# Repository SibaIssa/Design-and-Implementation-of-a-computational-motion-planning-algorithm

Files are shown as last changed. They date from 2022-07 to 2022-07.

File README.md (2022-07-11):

# Design-and-Implementation-of-a-computational-motion-planning-algorithm-based-on-navier-stokes-equations
This repositoery is based on the graduation project for Bachelor Degree in Mechatronics Engineering at Tishreen University, Syria - Summer 2021

## Abstract
Formation of non-holonomic swarm robots has received a lot of considerations in both academia and
industry over last two decades. Many path planning methods produce collision-free paths for a group of
multiple robots, but many of them are computationally expensive and complex to implement and develop.
In addition, these methods do not find a solution in all environments, or they find a solution that is not
optimal. In this project, we present a computational motion planning algorithm based on fluid dynamics
PDE for Robotic Swarms. This proposed method features a computationally cheap algorithm, and it is
easy to develop using updated tools and hardware. But, most importantly, it always ensures finding a
path, because partial differential equations of fluid dynamics always finds a solution that describes the
movement of the fluid’s particles towards a goal. The aforementioned feature gives this algorithm a clear
advantage because it is reliable, and it produces a smooth path. The validity of this algorithm will be
tested on a robotic swarm platform that we designed and implemented to ensure high quality and ease of
use. The control of the swarm is preformed centrally, and a visual feedback is provided continually to the
central computer from a camera that is fixed above the robots.

## Environment Setup
In the end we will have a square platform (**4.2×4.2 [m²]**) with high walls and different types of obstacles. Above the platform there is a fixed **stereo camera**, and inside the platform there will be a **15 mobile robots**. We will design everything from scratch then we will test our proposed path planning algorithm on our designed platform. And this is a 3D design for the platform:

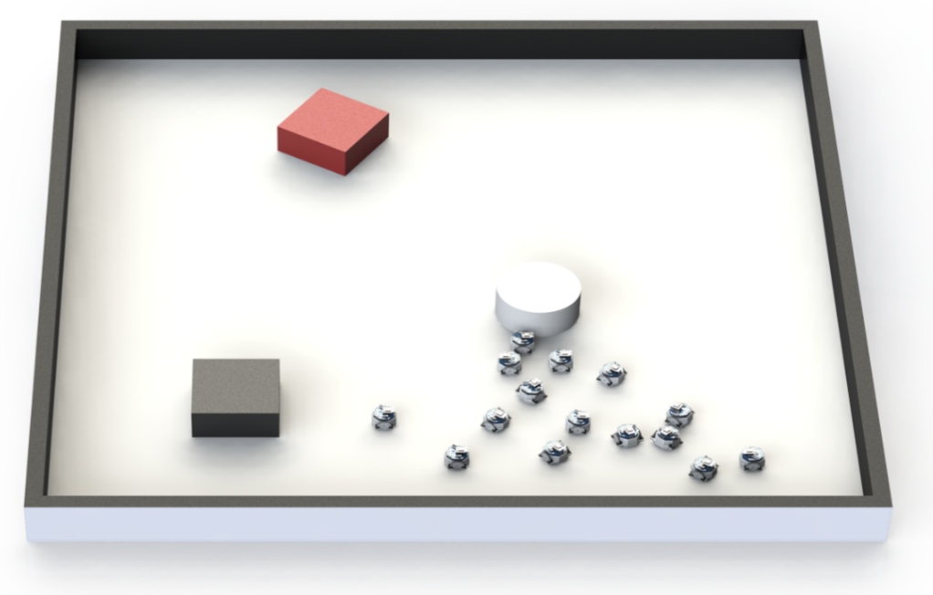
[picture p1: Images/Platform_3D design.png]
platform


## Project overview

### Designing Stage:

After many designs, we ended up with the octagon-shaped robot with two circuits (each one of them has two layers). We chose this design; because it was the most compact one. We used **SolidWorks** for designing the body while we used **Altium** for the circuits. 

- circuits PCB design (the left circuit is the top one while the right circuit is the bottom one):

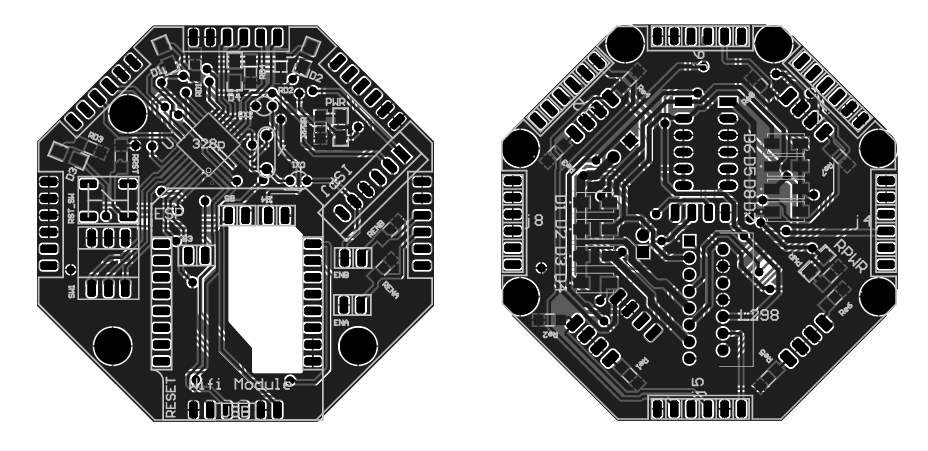
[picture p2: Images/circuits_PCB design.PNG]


- We can see below the body CAD design with the wheels in which we chose them like this to make our own encoder and it is important to mention that we chose the optimum number of the holes (33 holes):

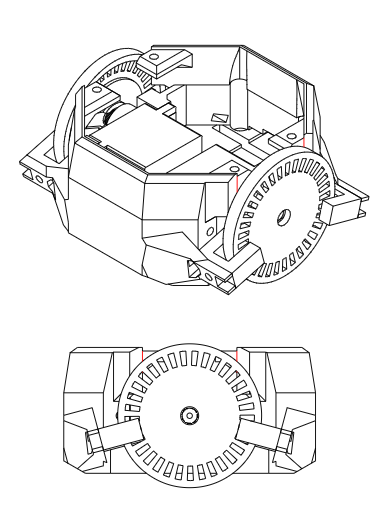
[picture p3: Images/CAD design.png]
CAD


- robot top-view:

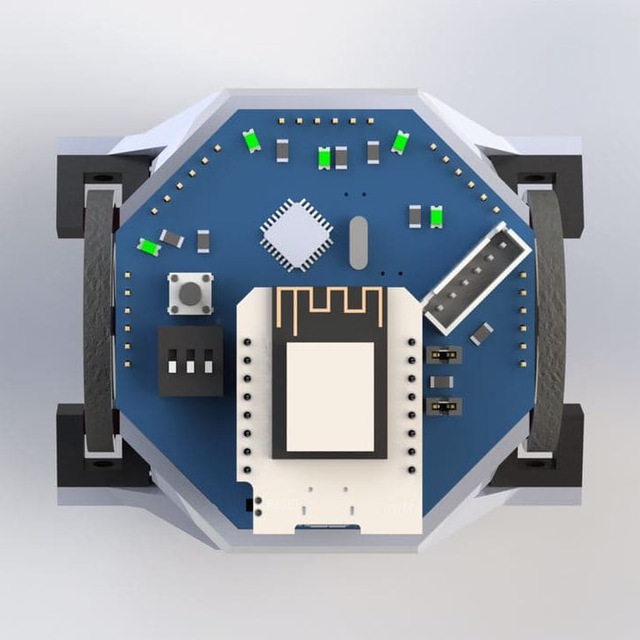
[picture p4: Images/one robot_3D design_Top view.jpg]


### Manufacturing stage:
After the designing stage, we started printing the bodies and the wheels by using a 3D printer (we used Acid Polylactic with PLA as a material). And we were printing the circuits in parallel.

- circuits after manufacturing:

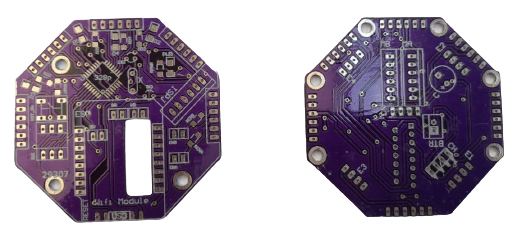
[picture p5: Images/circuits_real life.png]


- we can see below one robot after manufacturing and assembling, and for more images about manufacturing stage you can check the [Images Folder](https://github.com/SibaIssa/Design-and-Implementation-of-a-computational-motion-planning-algorithm/tree/main/Images).

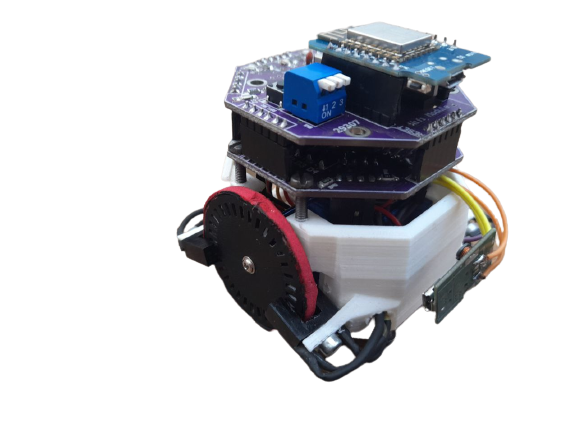
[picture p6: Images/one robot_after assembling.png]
robot


### Algorithm Implementation
- We started in simulation; we implemented the PDE algorithm for one robot and tested it on different maps by using **MATLAB**. And as we can see below the PDE algorithm managed to find a path from the start point to the goal in each map:

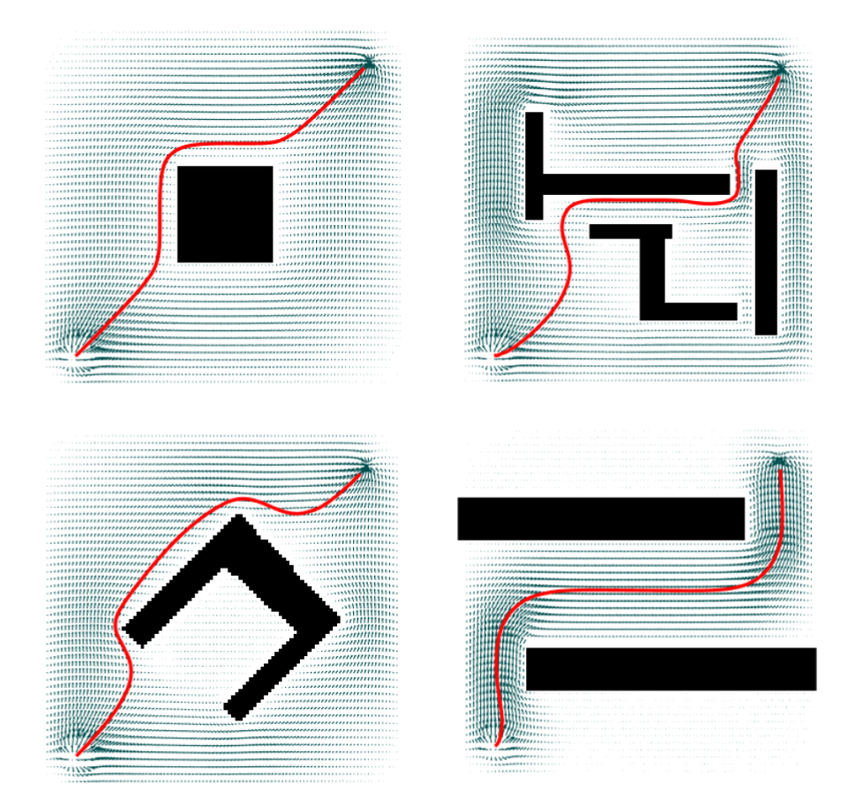
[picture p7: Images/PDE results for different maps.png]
different_maps


As it is clear from the previous image; the PDE managed to find the path for any given map which gives it advantages over the most popular path planning algorithms (A*, Dijkestra and potential field) in terms of finding the path and time consumption.

- Then we started the impelmentaion in real life:
1. We calibrated the camera depeding on the pinhole camera model and we found the Intrinsic and Extrinsic parameters.
2. We used Aruco markers in order to identify each robot, and each robot has its own ID through the whole project; in which it will help us later in sending a specific message for each robot.
3. After working onthe feedback system, we started working on ROS on the central computer. We created three nodes each one has it is clear task -as it is clear below- then we connected the central computer with each robot wirelessly by using esp8266 chip.

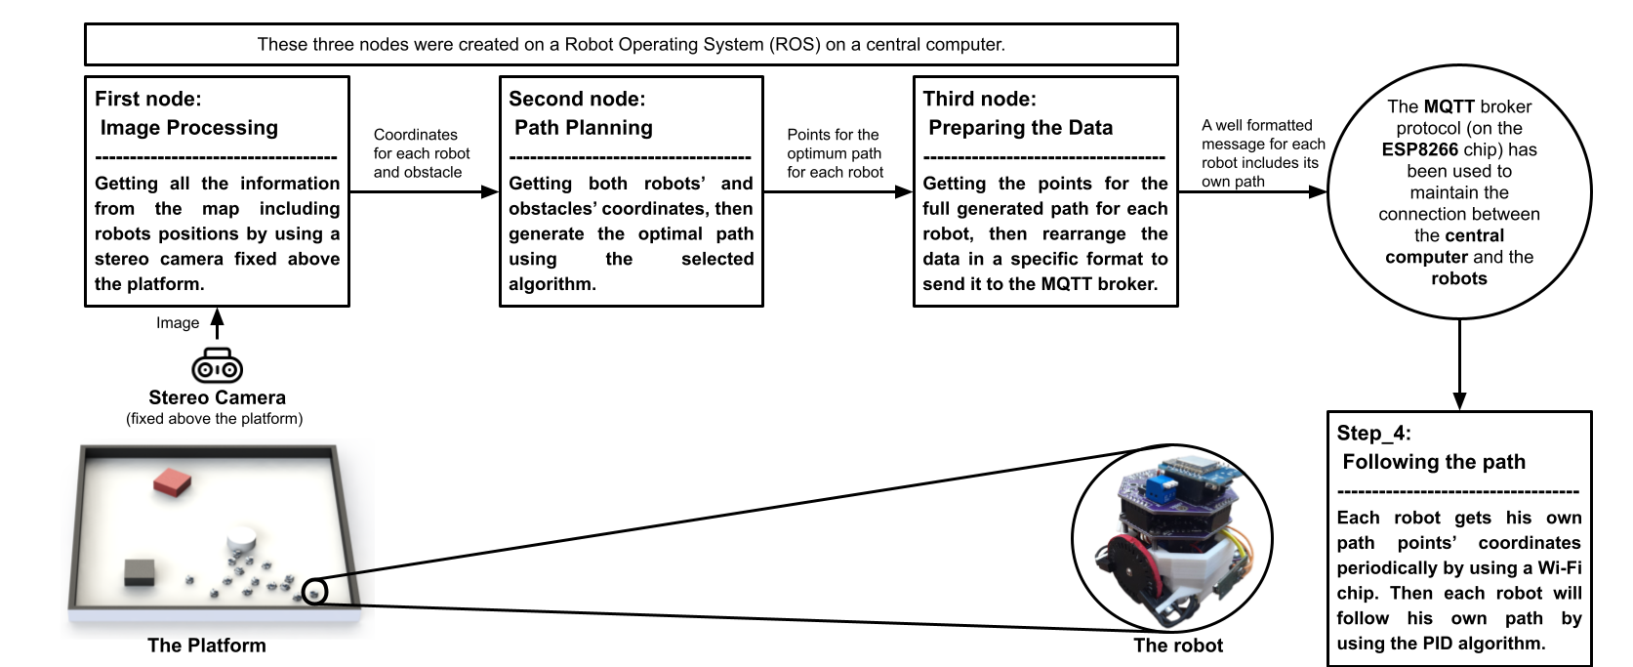
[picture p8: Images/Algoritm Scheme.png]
here the project scheme:
 
## Project output
1. Platform (**4.2×4.2 [m²]**) with high walls and different types of obstacles.
2. **15 octagon-shaped mobile robots**  designed from scratch with dimensions (**6×7×6 [m³]**).
3. Implementing a computational motion planning algorithm on a single robot, then developing it and expanding it for the swarm of robots.
4. Comparing between our suggested algorithm and the famous algorithms in the literature (A*, Dijkstra, Potential Field) 
5. Extracting results that confirm the validity of the proposed algorithm and its superiority over conventional and non-traditional algorithms in terms of path-finding inevitability and other factors. You can check the following video:

https://user-images.githubusercontent.com/51207510/178347807-7e33a0b5-0230-4640-b8dc-26850cdf5a6b.mp4

## Files
- [Body Design Folder:](https://github.com/SibaIssa/Design-and-Implementation-of-a-computational-motion-planning-algorithm/tree/main/Body%20Design)
includes **SolidWorks** files.
- [Circuits PCB Design Folder:](https://github.com/SibaIssa/Design-and-Implementation-of-a-computational-motion-planning-algorithm/tree/main/Circuits%20PCB%20Design)
includes the **PCB** files for both top and bottom circuits, and it is important to metion that we used **Altium** software for designing the circuits.
- [Swarm Robot Firmware Folder:](https://github.com/SibaIssa/swarm-robot-firmware) includes **.cpp** files in which contain the code that we put it on the microcontroller on each robot, and we used **AVR** software for programming.

## Credits
I worked on this project with two of my colleagues:
- [Adnan Saood](https://github.com/adnan-saood)
- [Nada Salman](https://www.linkedin.com/in/nada-s-salman/)

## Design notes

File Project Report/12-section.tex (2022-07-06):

لإيجاد مواقع الروبوتات سوف يتم استخدام نظام التعريف ArUco، حيث تتم طباعة عدة QR codes ولصقها على سطح كل روبوت. بعد القيام بعملية معايرة لبارامترات الكاميرا الـIntrinsic والـExtrinsic يمكن أيجاد المصفوفة $ \mathbb{C} $ المستخدمة في \ref{eq:cameramatrix}.

\begin{equation}\label{eq:cameramatrix}
\mathbb{P}=\left(\begin{matrix}p_x\\p_y\\1\\\end{matrix}\right)=\mathbb{C}\times\left(\begin{matrix}r_x\\r_y\\r_z\\1\\\end{matrix}\right)=\mathbb{C}\times\mathbb{R}
\end{equation}
حيث يمثل $ \mathbb{P} $ موضع الروبوت في إحداثيات حساس الكاميرا، و$ \mathbb{R}  $إحداثيات الروبوت في الاحداثيات الأرضية، و$  \mathbb{C}  $ مصفوفة الكاميرا (Camera Matrix).

منها يمكن نقل كل بكسل من بكسلات الكاميرا الى الاحداثيات الأرضية باستخدام الـpseudo-inverse للمصفوفة $\mathbb{C}$. نذكر هنا أن المصفوفة $ \mathbb{C} $ :

\begin{equation}
\mathbb{C}=\mathbb{K}\times\left(\mathbb{R}\ |\ {T}\right)
\end{equation}

حيث تمثل المصفوفة $ \left(\mathbb{R}\ |\ {T}\right)  $ التحويل المتجانس الذي ينقل $ \mathbb{R}  $ الى احداثيات الكاميرا، والمصفوفة $ \mathbb{K}  $ تقاس من بارامترات العدسة والحساس وتشكّل كالتالي:
\begin{equation}
\mathbb{K}=\left(\begin{matrix}f_x&0&0\\s&f_y&0\\c_x&c_y&1\\\end{matrix}\right)
\end{equation}

يمثل كل من $ f_x, f_y $ البعد البؤري للعدسة، وs معامل انحراف الحساس، و $c_x, c_y$ يمثلان مركز الحساس بوحدات البكسل.
نذكر هنا أنه من الواجب القيام بعملية معايرة تسبق مرحلة نقل كل نقطة من نقاط الكاميرا الى الاحداثيات الواقعية وذلك لتقريب الكاميرا الموجودة أقرب ما يمكن الى نموذج الـ pinhole\ camera الموجود في المعادلات السابقة.

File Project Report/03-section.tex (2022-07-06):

تعد مضمنات هذا البحث أحد القضايا التي تطرق لها الباحثون بكثرة واهتمام في الفترة الأخيرة: التشكيل السرابي للروبوتات غير الهولنومية.  هناك العديد من الطرق التي قد توصل مجموعة من الروبوتات من منطقة الى أخرى في فضاء العمل بسلام (أحياناً)، لكن عديدها إما تحوي تعقيدات برمجية وبنية خوارزمية ومخطط حالة غاية في التعقيد، أو أنها لا توفر حل في أغلب الأحوال. نحاول في هذا البحث تقديم خوارزمية تخطيط مسار لسرب من الروبوتات الغير هولنومية في بيئة مكتظة باعتبارها تابعة بالحالة للحل الرقمي لمعادلة جريان المائع من منطقة إلى الأخرى بشكله المستقر.
من مزايا الحل المقدم أنه رخيص حسابياً ويمتلك العديد من العناصر القابلة للتسريع باستخدام أدوات حسابية وعتاد حاسوبي جديد، لكن محور البحث يكمن في مكان آخر. نحاول في هذا البحث تقديم طريقة حتمية لإيجاد مسارات حركة هذه الآليات من منطقة لأخرى في فضاء العمل، فالمعادلات الرياضية لجريان السوائل حتماً ستجد حلاً يقوم بإيصال جزيئات المائع من المنطلق للهدف. هذه الحتمية ستعطي أفضلية واضحة للطريقة المقترحة لسببين: موثوقية الطريقة (إذا كان الوصول ممكن فهو حتماً ضمن مجموعة الحل)، ونعومة المسارات المنتجة (مما سيمكن الآليات الغير هولنومية من تقليص الفارق العتادي مع الهولنومية).
سيتم اختبار طريقة الحل المقترحة على منصة روبوتات قمنا بتصميمها وتنفيذها بشكل كامل، مع مراعاة عوامل مثل جودة التصنيع والمرونة والسهولة في الاستخدام والتعديل والتكلفة المناسبة. تم تصميم المنصة بحيث أن يتم التحكم والتواصل مع الروبوتات بواسطة حاسوب مركزي ويتم مراقبتها بواسطة كاميرا مُثبتة أعلى المنصة.

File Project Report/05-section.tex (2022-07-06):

إنّ مفهوم الأسراب مأخوذ من الطّبيعة، حيث تمّت محاكاة أسلوب التّعاون بين الأسراب البيولوجيّة (النّمل، النّحل، الأسماك..) ونُقل هذا المفهوم إلى الرّوبوتات. يمكننا تصنيف الأسراب البيولوجيّة إلى أسراب أرضيّة وأخرى جويّة، وكذلك الأمر بالنّسبة للرّوبوتات. يختلف هذان النّوعان فيما بينهما من ناحية التّطبيق بشكل أساسي وقد اعتمد البحث \cite{b1} على تصنيف التطبيقات حسب نوع المهمّة الّتي تتولّاها الرّوبوتات (تغطية منطقة ما، مهمّات خطيرة، مهمّات يلعب الوقت فيها دور أساسي...).
يعدّ تخطيط المسار الحسابي للروبوتات الأرضيّة مشكلة مطروقة جداً في الوقت الحالي لما لها من أهمية في توفير الوقت، الطاقة، والعتاد الحسابي. حسابياً، إنّ مشكلة تخطيط المسار الأمثل لأي آلية هي مسألة \textenglish{NP-Hard} \cite{b2,b3}. تتعقد أليات الحساب وتبعاته عند التعامل مع بيئة ديناميكية، أو عند القيام بتخطيط مسار أكثر من كائن في ذات الوقت.
يهدف المشروع الى البحث في إمكانية تطوير آليات لتخطيط المسار الحسابي لمجموعة كائنات اعتماداً على معادلات الجريان النّاتجة عن حل المعادلات التّفاضلية الجزئيّة لحركة الموائع. لقد قدّم كلّ من نافيير وستوكس معادلات كافية لنمذجة حركة السائل في الظروف المُختلفة، وسيتمّ الاعتماد عليها في إنشاء المسارات.

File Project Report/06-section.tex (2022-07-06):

يقدم هذا القسم مجمل ما تم مراجعته بهدف تصميم وتنفيذ خوارزمية البحث والمنصّة الفعالة.

\subsection{التصنيف والتصميم}

إنّ الأنظمة متعدّدة الروبوتات تلاقي اهتماماً كبيراً في المراجع ولاسيّما في الآونة الأخيرة؛ نظراً إلى أنّ مجالات التّطبيق والمهام الّتي تواجهها تزداد تعقيداً. لقد تمّ اقتراح تصنيف جديد في عام 2004 اعتماداً على ثلاث نقاط أساسيّة: (1) عقلانيّة التّصميم، (2) الوظائف التّقنيّة الاساسيّة (لكّل من العتاد الصّلب والبرمجيّات)، (3) المهمّات الّتي يجب أن تقوم الرّوبوتات بتنفيذها. حيث تمّ التّصنيف على عدّة مستويات ضمن فئتين أساسيّين: الأبعاد التنسيقيّة، وأبعاد النّظام كما هو موضّح في الجدول \ref{06:table:1} \cite{b4}. 

\begin{table}[]
	\begin{tabular}{|l|l|}
		\hline
		الأبعاد التّنسيقيّة Coordination Dimensions & أبعاد النّظام System Dimensions       \\ \hline
		التّعاون   Cooperative                      & الاتّصال   Communication              \\ \hline
		المعرفة Knowledge                           & تكوين   الفريق team Composition       \\ \hline
		التّنسيق   Coordination                     & هيكليّة   النّظام System Architecture \\ \hline
		التّنظيم Organization                       & حجم الفريق Team Size                  \\ \hline
	\end{tabular}
\caption{الأبعاد التنسيقية وأبعاد النظام}
\label{06:table:1}
\end{table}

وفي العام التّالي طرحت الورقة البحثيّة \cite{b5} تبين أنّ أي فعل يقوم به أي روبوت يَأخذ بالحسبان الأفعال الّتي تقوم بها بقيّة الرّوبوتات، وهكذا ينتج مجموعة من الرّوبوتات الّتي تعمل باتّساق لتحقيق أفضل أداء ممكن. وقد أظهرت هذه الآليّة من التّنسيق أداء عالٍ؛ حيث تمكّنت الروبوتات من اكتشاف بيئتها في وقت أقل مقارنةً مع المنهجيّات الأخرى الّتي لا تعتمد على التنسيق بين الرّوبوتات بشكل صريح. وبالرّغم من النّتائج الجيّدة الّذي حقّقها النّهج المتّبع في البحث \cite{b5}، إلّا أنّ هناك بعض النقاط الّتي تحتاج إلى تطوير، حيث يجب مناقشة الحالات الّتي يتمّ فيها تعطّل أحد الرّوبوتات أو حدوث تغيّر ما في البيئة المحيطة بها.

ومن ناحية أخرى، نالت أعداد الرّوبوتات الّتي تشكّل السّرب اهتماماً كبيراً في مجال البحث العلميّ. على الرّغم من أنّ سلوك كلّ روبوت على حدا يُعدّ سلوكاً بسيطاً، إلاّ أنّه عندما تعمل هذه الرّوبوتات معاً يصبح سلوكها أكثر تعقيداً. أشار \cite{b6} إلى أنّ فهم الرّوبوتات بشكل فرديّ هو أمرٌ سهل، أمّا بالنّسبة لتوقّع سلوكها معاً فهو أمرٌ صعب المنال. لقد تمّ عرض النّهج المعتمد من قبل \cite{b6} من خلال التّحليل العميق لخوارزميّة السّرب المُتّبعة والنّموذج الاحتمالي المُرتبط بها؛ حيث تمّ فحص خوارزميّة التّحكم باستخدام فضاء الحالة المُطوّرة من قبل \cite{b7} على مجموعة من الرّوبوتات الباحثة عن طعام.

 لقد قام \cite{b6} باستخدام خوارزميّة ألفا في شبكة الاتّصال اعتماداً على المنطق الزّمني $ (Temporal logic) $، حيث تمّ التّركيز على حالة الرّوبوتات بدلاً من الموقع وتفاصيل حركة كلّ روبوت. ولكنّ وبالرّغم من النّتائج المُرضية وصل اليها البحث، إلا أنه لم يتمكّن من إجراء عملية التّحليل سوى على عدد قليل من الرّوبوتات بسبب مشكلة انفجار الحالة $ (state explosion) $ التي ظهرت أثناء عمليّة فحص النّموذج الرّياضي. 
 
 \subsection{تخطيط المسار}
 
 تُعدّ مشكلة تخطيط المسار متعدد الروبوتات مشكلة معقدة حسابياّ لأنّ صعوبة الحساب تنمو مع عدد الروبوتات. إنّ وجود قيود وعوائق في المسار يولّد مشكلة كبيرة، ومن هنا بدأت عمليّة البحث عن خوارزميّات لحلّ هذه المشكلة. أحد الخوارزميّات المُتّبعة لحلّ مشكلة المسار المقيّد هي الـ \textenglish{Visibility Graph (VG)}. تبدأ هذه الطريقة بتشكيل الرّسم البياني عن طريق رسم العقد (Nodes) والحواف (Edges) باستخدام تقنيّة التّصوير بالأشعّة، ومن ثمّ تحديد البيان الموجّه. يتمّ بعد ذلك إيجاد المسار الأقصر باستخدام خوارزميّات إيجاد الطريق الأقصر في البيان. نذكر هنا أن المسار النّاتج عادةً قريب جدّاً من العوائق.
 
 وكان البحث \cite{b8} قد قدّم عام 1985 طريقة فريدة لتفادي العوائق اعتماداً على تقنيّة الـ $ (Potential Field) $، حيثُ تمّ التّحكم بالروبوتات على عدّة مستويات وبالزّمن الحقيقي. وتتميّز هذه الطريقة بإمكانيّة توسيع الحلّ ليشمل البيئات ذات العوائق المُتحرّكة باستخدام حقل كموني متغيّر مع الزّمن.  وفي عام 2006 قدّم العمل \cite{b9} طريقة حقل كموني لتخطيط مسار الروبوت بالاعتماد على ناتج جمع تابعين هما: تابع $ (repulsive) $ الذي يتجنب المسارات القريبة من العوائق، وتابع $  (Attractive) $ قيمته تتعلق بالمسافة عن الهدف.
 
 إنّ طريقة الـ $ potential field $ هي طريقة مباشرة لحساب الحقل المتجهات $ (vector field) $ اعتماداً على موقع الهدف والعوائق، ولكنها تتطلّب روبوتات مُتحكّم بها بشكل كامل (قادرة على التّحرك بأي اتّجاه بشكل آني). على خلاف الحقل الكموني، طرق تخطيط المسار المعتمدة على الدّوال التّدفقيّة $ Stream function $ لا تتطلب التّحكم ذلك، كما أنّها تضمن تحوّل جميع نقاط التّوازن إلى نقاط سرجيّة، مما يعني ضمان وصول الروبوت إلى هدفه. لقد أظهرت عمليّة تخطيط المسار المُعتمدة على الدّوال التّدفقيّة المطروحة في \cite{b10} فعاليّة وسرعة عاليّة في التّكيف مع التّغيرات في الشّروط. على عكس طرق تخطيط المسار الأخرى، الطّرق الّتي تعتمد على الدّوال تتميز بمظهرها الحدسيّ بالنّسبة لمراقب الخارجي. إنّ وجود أكثر من حاجز لا يضمن دائماً الحصول على نتائج صحيحة، لكن هذا المثال يوضّح أن السلوك لا يزال مقبولاً كما هو موضح في الشكل \ref{06:fig:1}.
 \begin{figure}[h]
 	\centering
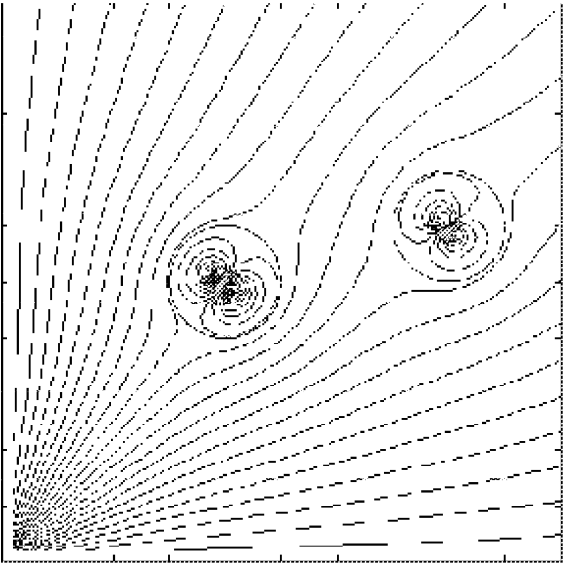
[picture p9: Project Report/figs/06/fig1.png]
 	
 	\caption{مثال على الدوال التدفقية}
 	\label{06:fig:1}
 \end{figure}

في عام 2015 تمّ طرح سلالات فورونوي \textenglish{VORONOI STRAINS} كخوارزميّة جديدة لتخطيط المسار والّتي حقّقت فائدة مهمّة على صعيد البيئات المعقّدة \cite{b9}. لقد حقّقت هذه الخوارزميّة نتائج مثيرة للاهتمام في مساحات عمل فيها عدد كبير من العوائق، فقد أظهرت حلولاً أفضل بكثير من خوارزميّة PSO البسيطة والمُطوّرة من أجل نفس عدد التّكرارات. إضافة إلى ذلك، أثبتت أنّها أكثر صلادة وأقل اعتماديّة على الحالة الابتدائيّة (العشوائية). كما تتميّز هذه الخوارزميّة باحتماليّة أكبر لتجنّب النّقاط الصّغرى المحليّة، ولكن قد أثبتت التّجارب أن عمليّة االأمثلة هذه غير مُجدية مالم تكن البيئة معقّدة بشكل كافِ.

أثناء تخطيط الحركة يمكننا تصنيف العمل إلى صنفين أساسيّن؛ فإمّا أن يتمّ تخطيط المسار بشكل كامل قبل البدء بالحركة (offline)، أو أن تتمّ عمليّة التّخطيط بشكل تدريجي أثناء الحركة (online).

  في \cite{b11} ، تم التّركيز على تخطيط المسار بشكل كامل قبل بدء الحركة، بالإضافة إلى وجود حواجز ثابتة، وهي إحدى الأمور الّتي أعطت هذا البحث محدوديّته. تتميّز طريقة تخطيط المسار المُقترحة في \cite{b11} بأنّها تمكّننا من الحصول على مسار ثلاثي الأبعاد مثالي يمكن الروبوتات من التحليق على ارتفاعات منخفضة في بيئة ذات تضاريس مُعقّدة.
  
  وفي عام 2020 طُرحت الورقة البحثيّة \cite{b12} بهدف توجيه روبوتات طائرة في مجال جوّي مفتوح وتضاريس غير معلومة لتتفوق بذلك على البحث \cite{b11} وذلك عبر حلّ معادلة الاستمراريّة للموائع. لقد حقّقت هذه الدّراسة وقتاً أقلّ من أربع طُرق أخرى $( A*, Dijkstra, DP, PE) $.
  
  إضافة إلى الخوارزميات التقليدية، العديد من الدراسات أظهرت نتائج خوارزميات التعلم الآلي لحل هذه النوع من المشكلات. في \cite{c1} تم استخدام الشبكات العصبونية الالتفافية لتحسين حلول الخوارزميات التقليدية كما نجد في \cite{c2} أنه تم استخدام خوازرمية تعلم Q-learning معتمدة على الخوارزمية المحسنة \textenglish{improved particle swarm optimization}. تهدف الخوارزميات المستخدمة الى تقليل طول المسار وزمن الوصول وزوايا دوران الروبوتات لتقليل استهلاك الطاقة. تمت المقارنة بين اربع خوارزميات وايجاد النتائج باختلاف عدد الروبوتات في السرب هي CQL و PSO وIPSO-DV  و QIPSO-DV وأظهرت النتائج تفوق QIPSO-DV على باقي الخوارزميات كما يمكن ملاحظة تراجع أداء هذه الخوارزمية مع زيادة عدد الروبوتات ولاسيما من حيث زمن التنفيذ وعدد التكرارات اللازمة للوصول الى الحل الأمثل (إن وجد) .
  في \cite{c3} تم اقتراح تقسيم الخريطة الكلية الى خرائط بيان جزئية sub-graphs مع قيود على الدخول والخروج من كل خريطة وذلك لضمان إيجاد المسار. بعد التجريب، تم التوصل الى حل فعال وسريع نسبيا لكنه لا يضمن ايجاد مسار أمثل وبحاجة إلى عمليات معالجة لاحقة لتقليل المسافات الضائعة.  
  
   يعد موضوع انشاء طريق باستخدام الحل الرقمي للمعادلات التفاضلية الجزئية موضوع حديث عالمياً ويحتاج الكثير من العمل، قدمت واحدة من الأبحاث القائمة على موضوع استغلال جريان السوائل في توليد المسار عام 2017، حيث تهدف \cite{b13} الى انشاء المسار الأفضل لحركة سفينة باستخدام طريقة $ lattice Boltzmann $ الرقمية. البحث لم يناقش آلية انشاء طريق من نقطة إلى اخرى في فضاء العمل، بل ناقش عبور منطقة تحتوي عوائق بشكل عام. إضافة لذلك، فإن الحل الرقمي باستخدام $ lattice Boltzmann $ لم ينتج حقول متجهات سرعة تحمل نفس السلوك الفيزيائي للسوائل، يمكن التحقق من ذلك بالنظر في سلوك الحقل عند الحواجز في الشكل \ref{06:fig:2}.

   \begin{figure}[htbp]
   	\centering
   	\includesvg[width=0.85\linewidth]{figs/06/fig06_2}
   	\caption{التدفق المولد باستخدام الخوارزمية $ lattice Boltzman $. يمكن ملاحظة السلوك غير الفيزيائي للسائل بالنظر الى تداخل السائل مع الجدران.}
   	\label{06:fig:2}
   \end{figure}

      وكان قد طُرح في عام 2009 نظام  قوي وسريع لتخطيط المسار للملاحة الآليّة \cite{b14}، والفكرة الأساسيّة الّتي اعتمد عليها هذا البحث هي انشاء المسار عبر نشر موجتين متتاليتين، كما في الشكل \ref{06:fig:3}. تبدأ بموجة أولى تكون ذات سرعة قليلة نسبيّاً تُمكّن الرّوبوت من نقل طوبولوجيا الخريطة إلى الحاسوب، بينما تنتقل الموجة الثّانية ذات السّرعة العالية في الخريطة وذلك من أجل تكوين مسار من نقاط جهات الانتشار ذات التّقعّر الأعلى. وفي النّهاية يمكن التّحكم في المسارات المثلى المخطّطة اعتماداً على معامل واحد: المسار الأقصر، الأكثر أماناً، أو الهجين.
       \begin{figure}[h]
      	\centering
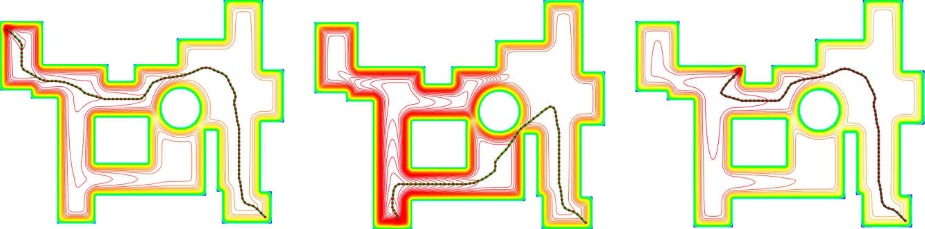
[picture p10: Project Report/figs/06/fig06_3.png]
      	
      	\caption{الأمواج المتقدمة والمتأخرة في العمل\cite{b14}}
      	\label{06:fig:3}
      \end{figure}

      \subsection{الاتصال}
      
      كما أشرنا سابقاً، فإنّ فكرة الاسراب مأخوذة من الأسراب البيولوجيّة، حيث أن أساس التّحكم في سلوك هذه الأسراب هو تبادل المعلومات. يتمكّن الأفراد في الاسراب البيولوجيّة من تبادل المعلومات بشكل مباشر عن طريق المجسّات، الحركة، أو الصّوت. استوحى \cite{b15} تصنيف أسراب الرّوبوتات من الاسراب البيولوجيّة، حيث تمّ التّصنيف إلى مجموعتين أساسيّتين:
            
      \begin{itemize}
      	\item \textbf{أولاً: التّفاعل عن طريق التّحسس:} هو الطّريقة الأبسط للتّواصل بين الرّوبوتات. تتطلّب من الرّوبوت التّمييز بين الأقران والبيئة المحيطة به. يطلق على هذا النّوع من الاتّصال بالصّريح. 
      	\item \textbf{ثانياً: التّفاعل عن طريق البيئة:} حيث تستخدم الرّوبوتات البيئة كوسيلة للتّواصل فيما بينها. يسمّى هذا النّوع بالتّواصل الضّمني. أسراب النّمل مثال شهير على الاتّصال الضّمني؛ حيث يتواصل أفراد السّرب عن طريق إفراز وتتبع مادّة الفيرومون \cite{b15}.
      \end{itemize}
      
      هناك العديد من طرق الاتّصال المستخدمة في أسراب الروبوتات، ومن التّقنيات المستخدمة للاتصال بين الرّوبوتات في السّرب الواحد (الأشعة تحت الحمراء، البلوتوث، الـWi-Fi، ZigBee، ...). تعد عمليّة اختيار التّقنيّة المناسبة مهمّة جدّاً لأنها مؤثر مباشر على أداء السرب، لذلك تتمّ بناءً على عدّة معايير (البيئة الّتي تعمل بها الرّوبوتات، مدى الاّتصال، معدّل نقل البيانات، ...) وقد قام العمل \cite{b16} بمقارنة أداء هذه الطّرق.
      
وعندما نتوجّه نحو الاتّصال اللاسلكي فإنّ شرائح الـ ESP8266 توفر ما يجعلها الخيار الأمثل، فهي منخفضة التّكلفة مقارنة بأدائها، وتدعم بروتوكولات TCP/IP بشكل كامل.  تتكون من SoC يحوي معالج Xtensa Tensilica [32bit]  وشريحة Wi-Fi تدعم بروتوكول  الاتّصال اللاسلكي IEEE 802.11b/g/n،  اضافة إلى العديد من الميّزات كما ورد في مقدّمة \cite{b17}.

مجتمع الـ Opensource الخاص بشريحة الـ ESP وفّر مكتبة PainlessMesh المبنية خصّيصاً لتشكيل شبكات تعتمد على أجهزةESP8266؛ حيث أنّها تبني شبكة خالية من الحلقات وتقوم بالتّحديث كلّ 3 ثواني. إلّا أنّه ومع الأسف كان هنالك انخفاض ملحوظ في أداء الشّبكة مع ازدياد العقد المُتّصلة بها كما كان واضحاً في نتائج التّجارب الّتي قام بها \cite{b17}.

بصورة عامة، تكمن الغاية الأساسية من تصنيع وتركيب الروبوتات بشكل عامة في الوظيفة التي ستقوم بها على أرض الواقع، ومن هنا يصبح للتنفيذ الفعلي أهمية كبيرة حيث أن محاكاة أداء الروبوتات ومهما كان دقيقا، فإنه يستخدم فقط لتقييم التصميم قبل التنفيذ الفعلي.
عالمياً، نجد تنوع كبير في منصات أسراب الروبوت وفق الغاية منها، بعضها تكون لأهداف تعليمية والبعض الآخر لأهداف بحثية لختبار صحة الخوارزميات كما في بحثنا هذا. تقدم \cite{c4} مراجعة عامة لأهم وأشهر منصات أسراب الروبوت ومقارنة من حيث الخصائص العامة والحجم والسعر والحساسات المستخدمة. تم التوصل إلى أن معظم هذه المنصات مناسبة جدا للأغراض البحثية، كما أن بعض المنصات مثل MarXbot وsbot وPheeno مناسبة للاستخدام على أرض الواقع وذلك لمرونة التصميم وإمكانية عبورها ضمن البيئات الصعبة. نجد في الجدول ملخصاّ عن المقارنة بين المنصات.

\begin{table}[]
	\begin{tabular}{@{}lp{10pt}p{10pt}p{10pt}r@{}}
		\toprule
		& التكلفة (دولار)          & الحجم (سم)               & عمر البطارية (ساعة)   & \multicolumn{1}{c}{الخصائص المميزة}                                                     \\ \midrule
		Colias \cite{c5}   & 25                      & 4                        & 4                     & وحدة استشعار بالأشعة تحت الحمراء ذات مدى   طويل                                         \\
		AmiR \cite{c5}    & 65                      & 6.5                      & 2                     & حساسات ذات درجة حساسية عالية                                                            \\
		Kilobot \cite{c6}  & 14                      & 3.3                      & 3                  & دواليب ذات حركة بنمط Omni                                                               \\
		R-one \cite{c7}     & 220                     & 10                       & 6                     & قابلة للتغير بشكل ذاتي، آلية اقتران                                                     \\
		s-bot \cite{c8}    & -                       & 15                       & 1                     & آلية اقتران، قابلية تجمع بشكل ذاتي،   كاميرا متحركة بكل الاتجاهات                       \\
		e-puck \cite{c9}    & 1200                    & 75                       & 2                     & يمكن محاكاتها باستخدام محاكي WEMBOTS و ENKI                                             \\
		MarxBot \cite{c10}  & -                       & 17                       & 8                     & قابلة للتغير بشكل ذاتي، آلية اقتران،   كاميرا متحركة بكل الاتجاهات، تصميم ببنية معيارية \\
		Pheeno \cite{c11}   & \multicolumn{1}{l}{270} & \multicolumn{1}{l}{12.7} & \multicolumn{1}{l}{-} & آلية قبض، كاميرا                                                                        \\ \bottomrule
	\end{tabular}
\end{table}

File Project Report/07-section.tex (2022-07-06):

\begin{itemize}
	\item تصميم وتنفيذ روبوتات صغيرة الحجم وعالية الجودة وسهلة الاستخدام.
	\item تصميم منصة عمل مناسبة تمكننا من اختبار أي خورازمية تخطيط مسار ضمن بيئة عمل معروفة سابقاّ.
	\item تطوير وبرمجة خوارزمية تخطيط حسابي تعتمد على المعادلات التفاضلية الجزئية لروبوت واحد ولسرب من الربوتات.
	\item  برمجة خوارزميات شهيرة أخرى في تخطيط مسار الروبوت لروبوت واحد ولسرب من الروبوتات.
	\item استخلاص نتائح تؤكد صحة الخوارزمية المقترحة وتفوقها على الخوازميات التقليدية وغير التقليدية من ناحية حتمية إيجاد المسار وعوامل أخرى.
\end{itemize}

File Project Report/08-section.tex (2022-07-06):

يوضح المخطط التالي آلية كاملة لعمل المشروع. نبدأ من عرض البينة البرمحية الموجودة على الحاسوب المركزي والتي تتكون من نظام تشغيل روس مكون من ثلاثة عقد تتصل مع بعضها بتقنية \textenglish{Publish / Subscribe}، ثم نوضح تواصل هذه النظام مع مخدم بروتوكول MQTT المسؤول عن تحقيق التواصل مع الروبوتات حيث تشترك الربوتات بـ topic التي تحوي الرسائل الحاملة لنقاط المسار. بالنسبة للنظام البرمجي الموجود على كل من الروبوتات، تستقبل شريحة الاتصال الرسالة من المخدم وتنقلها إلى المعالج ليثيوم باتباعها وفق خوارزمية التصحيح. أنظر الشكل \ref{fig:08-graph}.

\begin{figure}
	\centering
	
	\caption{}
	\label{fig:08-graph}
\end{figure}

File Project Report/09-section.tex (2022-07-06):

بعد أن قدمنا معلومات عن خلفية البحث والدراسات المرجعية وعرضنا مخططاً يوضح آلية عمل المشروع بكامل أجزائه،  ننتقل إلى الفصل الثاني لشرح الدراسات النظرية والنمذجة والمعادلات الرياضية المستخدمة وذلك بما يتضمن خوارزميات تخطيط المسار ونظام الاتصال بشكل أساسي. نفدم في الفصل الثالث المعلومات الكاملة عن عملية تصنيع الروبوتات بما في ذلك اختيار القطع الكهربائية والالكترونية وتصنيع الدارات وطباعة الأجسام كما نذكر شرحاً تفصيلياً عن نظام العمل البرمجي المُطور لتشغيل الروبوتات والحاسوب المركزي. في الفصل الرابع نقدم شرحاً عن النتائج التي توصلنا إليها حتى الآن.

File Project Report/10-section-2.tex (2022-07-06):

يمكن تصور تعميم الخوارزميات السابقة لسرب من الروبوتات بشكل مبسط بالشكل الآتي: نقوم بحساب المسار الأمثل لكل روبوت على حدى باعتبار كل بقية الروبوتات على أنها عوائق، وإعادة توليد هذه المسار بشكل مستمر باستخدام التغذية الراجعة من الكاميرا، ولكن وبسبب طبيعة هذه عمل هذه الخوارزميات لا يمكن تطبيق هذا المفهوم البسيط على أرض الواقع. فكما نجد في \cite{d7} عند استخدام خوارزمية A* لتوليد مسار لسرب من الروبوتات، تطلب التطبيق عدة عمليات معالجة لاحقة وتنظيم لحركة الروبوتات لمنع التصادم، كما تمت الحاجة لتصميم وحل مسألة برمجة خطية لتقليل طول المسار وزمن الوصول.
بالحالة العامة وفي معظم مسائل تخطيط المسار لسرب روبوتات، الهدف هو إيصال كل روبوت من نقطة البداية إلى نقطة الهدف بدون حدوث أي تصادم. كما وجدنا في الدراسة السابقة، فإن الكثير من الدراسات السابقة تعتمد تحسينات على خوارزميات تخطيط المسار التقليدية. في \cite{d7} تم تقدم تقديم خوارزمية جديدة تسمي البحث المعتمد على التصادم\textenglish{ Conflict Based Search (CBS)} وهي طريقة مثلى تتكون من مرحلتين ،مرحلة عالية المستوى ومرحلة منخفصة المستوى. في المرحلة المرتفعة المستوى، يتم البحث في ما يسمى شجرة التصادم\textenglish{ Conflict Tree(CT)} وهي شجرة تُبنى بناء على التصادك بين الروبوتات والعوائق، كل عقدة في الشجرة تمثل مجموعة قيود على حركة الروبوتات. في المرحلة المنخفضة المستوى، تتم عملية بحيث سريع بما يحقق القيود المطروحة في الطبقة العالية المستوى. في معظم الحالات تحقق هذه الخوارزمية مسحاً لعدد أقل من العقد بالمقارنة مع A* وتحافظ في نفس الوقت على الأمثلية.

\subsection{تعريف مسألة CBS}

نعرف كل قيد على أنه ثلاثية بالشكل $ (a_i,\ v,\ t) $ حيث أن الروبوت $ a_i $ ممنوع من المرور بالعقدة v في الزمن t، خلال إيجاد الحل سيتم ربط كل روبوت بعدد من القيود ولاحقا يجب إيحاد مسار لكل روبوت بحيث يحقق كل قيوده
تعرف التصادم على أنه رباعية بالشكل $ (a_i,a_jو v,t) $ مما يدل على أن الروبوتات $ a_i $ و  $ a_j $ تشغل نفس العقدة v في الزمن $ t $. يكون الحل المكون من k  مسار (عدد الروبوتات هو k) صحيحاً عندما تكون كل المسارات خالية من أي تصادمات.
المرحلة عالية المستوى:

حيث يتم بناء شجرة CT وهي شجرة ثنائية كل عقدة منها تتكون من:

\begin{itemize}
	
	\item مجموعة قيود (N.constraints): كل قيد ينتمي لروبوت، عقدة الجذر لا تحتوي على أية قيود وكل عقدة ابن ترث قيود العقدة الأم وتضيف قيداً جديداً.
	
	\item حل (N.solution): مجموعة مسارات بعدد k، بحيث أن مسار كل روبوت يحقق القيود المفروضة عليه. يتم إيجاد هذه المسارات من خلال بحث في المرحلة منخضة المستوى.
	
	\item تكلفة كلية (N.cost): تكلفة مسارات كل الروبوتات. تسمى هذه التكلفة f-value   للعقدة N.
	
\end{itemize}

\textbf{إيجاد المسار وفق شجرةCT :}

تتم عملية البحث عن مسار كل روبوت في المرحلة منخضة المستوى وذلك بمعرفة جميع القيود، عند إيجاد المسارات (المسار الخاص بكل روبوت وفق قيوده) يتم اختبارصحتها. يتم الاختبار من خلال المرور على كل المواقع في كل الأزمنة والتحقق من عدم وجود أي روبوتين في نفس المكان والزمن.في حال تم العثور على تصادم، تتوقف العملية وننتقل إلى مرحلة حل التصادم.
حل التصادم:
عند حدوث تصادم من الشكل $ (a_i,a_j, v,t) $، نجد بديهياً أنه يجب لإضافة إما $ (a_i,\ v,\ t) $ أو $ (a_j,\ v,\ t) $ إلى قائمة القيود N.constraints. لضمان أمثلية الحل، يتم اختبار الحالتين وتنقسم العقدة N  إلى عقدتين ترثان قيود العقدة الأم وتضيفان قيد الربوبت الأول والروبوت الثاني على الترتيب. يوضح الجدول 1 خوارزيمة طريقة CBS للمرحلة عالية المستوى.

\begin{english}
	\begin{algorithm}[H]
		\DontPrintSemicolon
		
		\KwIn{MAPF instance}
		\KwOut{Your output}
		
		$Root.constraints \leftarrow \Phi$\;
		 $Root.solution \leftarrow$ find individual paths by low level procedure\;
		 $Root.cost = SIC(Root.solution)$\;
		 insert $RoottoOpen$\;
		
		\While{$Open \neq \Phi$}
		{
			 $P \leftarrow $ best node from Open;\;
			 Validate paths from open until a conflict occures\;
			\If{P has no conflict}
			{
				 Return P.solution
			}
			 $C \leftarrow first conflict (a_i, a_j, v,t) in P$\;
			
			\ForEach{$ agent a_i in C $}
			{
				 $A \leftarrow new node$ \;
				 $A.constrains \leftarrow P.constraints + (a_i, v, t)$\;
				 $A.solution \leftarrow P.solution$\;
				 Update $A.solution $ invoking low level $a_i$\;
				 $A.cost \leftarrow SIC(A.solution)$\;
				\If{$A.cost < \inf$}
				{
					
					 Insert A to Open\;
				}
			}
		}
		\caption{High Level CBS}
	\end{algorithm}

\end{english}

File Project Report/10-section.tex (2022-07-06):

\subsection{الخوارزميات المعتمدة على البيان}

تعتمد هذه الخوارزمية على فضاء العمل لإنشاء بيان يمثل كل الأماكن المتاحة في فضاء العمل متضمناً نقطتي البداية والنهاية. يضمن هذا التمثيل ترميز وجود كل الطرق المتاحة وكذلك يضمن آلية لتفادي العوائق عن طريق حذف عقدها من البيان. بعد الانتهاء من التقطيع نعبر البيان من نقطة البداية الى النهاية باستخدام احدى خوارزميات عبور البيان الشهيرة $ (A^*, Disjkstra)$. يمثل الشكل \ref{fig:fig101} طريقة نقل فضاء العمل الى البيان.

\begin{figure}
	\centering
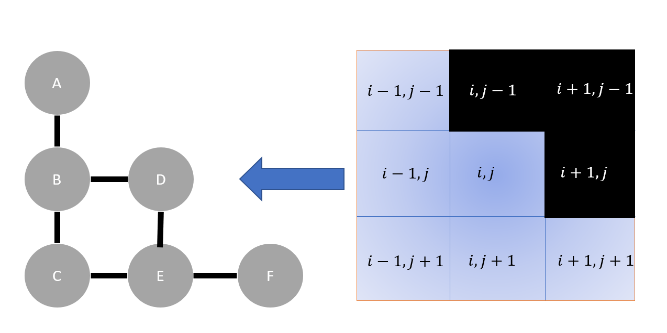
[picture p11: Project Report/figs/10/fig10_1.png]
	
	\caption{ تحويل فضاء العمل المقطع إلى بيان غير موجه}
	\label{fig:fig101}
\end{figure}

\subsubsection{المسار باستخدام A*}

خوارزمية عبور بيان وانشاء مسار تستخدم في كثير من مجالات علم الحاسوب نظرً لكمالها، مثاليتها، وكفاءتها. في الأنظمة التي من الممكن حساب الطريق بشكل استباقي، يمكن تجاوز أدائها من قبل الخوارزميات التي تستطيع حساب المسار قبل البدء بالتنفيذ \cite{d1} . واحدة من أكبر مشاكلها هي تعقيدها المكاني:$  O\left(b^d\right) $.

\subsubsection{المسار باستخدام Dijkstra}

هي خوارزمية صممت لإيجاد المسار الأقصر بين عقدتين في بيان معين. تعتمد الخوارزمية على إيجاد الطريق من خلال عبور عقد البيان بالتدريج ثم حساب معاملات المسافة وإيقاف البحث في حال مواجهة عائق \cite{d2}

\begin{table}
	\centering
	\begin{tabular}{cc}
		
		\begin{subfigure}{0.4\textwidth}
			\centering
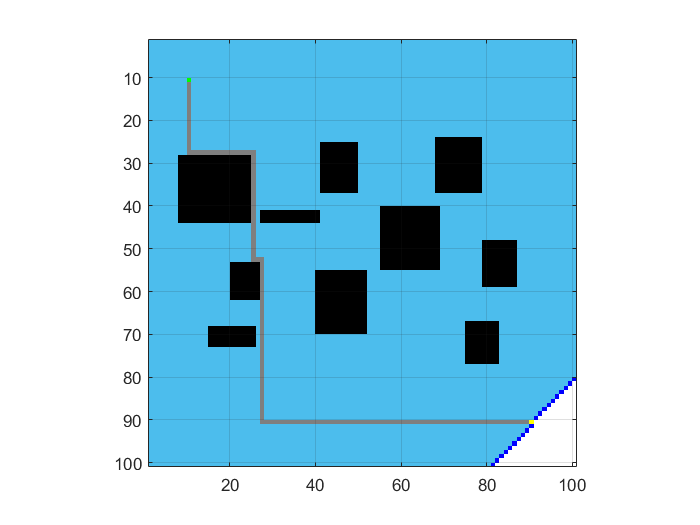
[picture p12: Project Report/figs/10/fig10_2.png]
			
		\end{subfigure}&
	
		\begin{subfigure}{0.4\textwidth}
			\centering
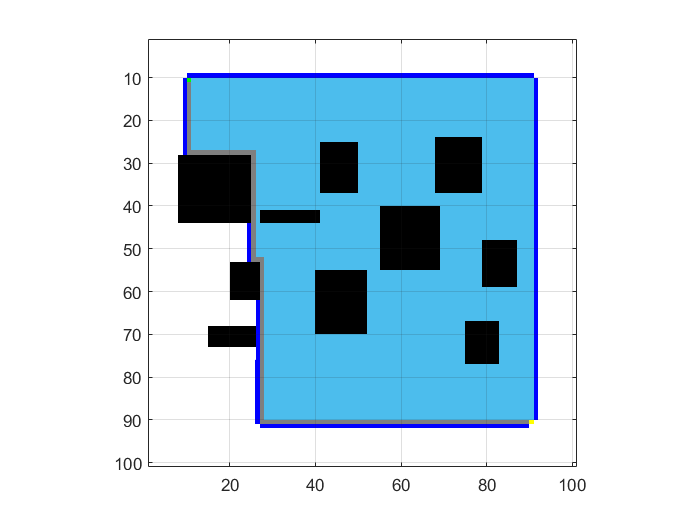
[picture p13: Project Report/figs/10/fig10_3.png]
			
		\end{subfigure}
	\end{tabular}
	\caption{خرائط لحل كل من خوارزميتي البيان.}
	\label{10:fig:graph}
\end{table}

\subsection{خوارزمية الحقل الكموني}
تعتمد خوارزمية \textenglish{potential field} على بناء خريطة افتراضية يتحرك الروبوت وفقها اعتماداً على مواقع المبدأ والهدف والحواجز. يمكن أن يتم حساب المسار اعتماداً على خريطة حواجز معروفة مسبقاً أو بالزمن الحقيقي اعتماداً على حساسات مثبتة على الروبوت أو على الحلبة. تم عرض هذه الخوارزمية لأول مرة عام 1985 \cite{b8} حيث قدم البحث الحقول $ potential field $ كجزئين، جزء جاذب وجزء منفر. الجزء الجاذب يقوم بسحب الروبوت نحو الهدف، أما الجزء المنفر يقوم بإبعاد الروبوت عن العوائق بمسافة أمان تحدد مسبقا. 

تستخدم هذه الخوارزمية بكثرة في تطبيقات تخطيط المسار وذلك لبساطتها وسهولة تطبيقها ولا سيما أنها تعطي نتائج جيدة في البيئات البسيطة التقليدية، لكن يوجد عدة سلبيات مرتبطة باستخدام هذه الخوارزمية.
أحد السلبيات هي أن الروبوت يمكن أن يحتجز في قيمة صغرى محلية مما يؤدي الى توقفه عن الحركة نهائيا وعدم وصوله الى الهدف. تم تطوير العديد من الطرق لحل هذه المشكلة متل تتبع الحائط   \cite{d4}  وإضافة حواجز افتراضية \cite{d5}. من السلبيات الأخرى هي عدم قدرة الروبوت على المرور بين حواجز متقاربة. عند عبور الروبوت بممر ضيق يقوم بحركة اهتزازية غير مستقرة نتيجة تأثره بقوى الحقل المنفر \cite{d6}.

\textbf{توليد المسار وفق $ potential field $:}

شعاع الحقل الجاذب يحسب من موقع الروبوت الى الهدف، أما شعاع الحقل المنفر يكون من موقع الحاجز الى موقع الروبوت. بجمع الشعاعين نحصل على شعاع يحدد اتجاهه اتجاه حركة الروبوت، ومطاله سرعة الروبوت. ليكن $ (x_r,y_r) $ موقع الربوت الابتدائي و $ (x_g,y_g) $ موقع الهدف و $ (x_o,\ y_o)   $ موقع الحاجز في خريطة ثنائية الأبعاد.

يعطى شعاع الحقل الجاذب بالعلاقات التالية:

\begin{equation}
{\vec{v}}_{attr}=\left(\begin{matrix}x_{atrr}\\y_{atrr}\\\end{matrix}  \right)
\end{equation}

\begin{equation}
\left(\begin{matrix}x_{atrr}\\y_{atrr}\\\end{matrix}  \right)=\left(\begin{matrix}x_{g} - x_{r}\\y_{g} - y{r}\\\end{matrix}  \right)
\end{equation}

تعطى المسافة والزاوية بين الروبوت والهدف بالعلاقات التالية:

\begin{equation}
d_o=\sqrt{\left(x_r-x_o\right)^2+\left(y_r-y_o\right)^2}
\end{equation}

\begin{equation}
\theta = tan^-1(\frac{y_r - y_o}{x_r - x_o})
\end{equation}

وبالتالي يعطى شعاع الحقل المنفر بالعلاقات التالية:

\begin{equation}
{\vec{v}}_{rep}=\ (\begin{matrix}x_{rep}\\y_{rep}\\\end{matrix})\ 
\end{equation}

\begin{equation}
x_{rep}=\frac{1}{d_o} cos(\theta), if d_o < s
x_red = 0 , otherwise  
\end{equation}

\begin{equation}
y_{rep}=\frac{1}{d_o} sin(\theta_o), if d_o < s
y_red = 0 , otherwise  
\end{equation}

حيث $ s $ هي قطر المنطقة الفعالية المحيطة بمركز الحاجز.
بجمع شعاعي الحركة الجاذب والمنفر نحصل على شعاع الحركة النهائي:

\begin{equation}
v_{final}^\rightarrow=v_{attr}^\rightarrow+v_{rep}^\rightarrow
\end{equation}

\begin{table}
	\centering
	\begin{tabular}{cc}
		
		\begin{subfigure}{0.35\textwidth}
			\centering
			\includesvg[width=0.9\linewidth]{figs/10/fig10_4}
		\end{subfigure}&
		
		\begin{subfigure}{0.35\textwidth}
			\centering
			\includesvg[width=0.9\linewidth]{figs/10/fig10_5}
		\end{subfigure}
	\end{tabular}
	\caption{عملية حساب المسار في طريقة الحقل الكموني}
	\label{10:fig:pf}
\end{table}

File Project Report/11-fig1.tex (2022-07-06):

\begin{center}
	\centering
\begin{table}[ht]
	\begin{tabular}{cc}
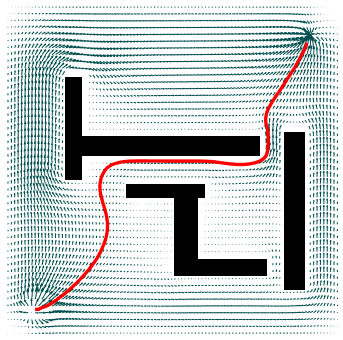
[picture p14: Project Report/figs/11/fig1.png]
		\begin{subfigure}{0.4\textwidth}\centering\caption{الخريطة الأولى}\label{11:fig:1}\end{subfigure}&
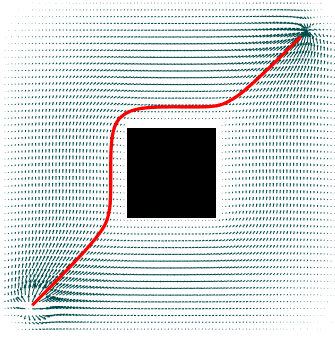
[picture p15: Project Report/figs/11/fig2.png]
		\begin{subfigure}{0.4\textwidth}\centering\caption{الخريطة الثانية}\label{11:fig:2}\end{subfigure}\\
		\newline
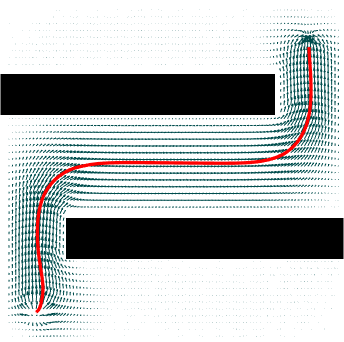
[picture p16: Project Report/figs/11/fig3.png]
		\begin{subfigure}{0.4\textwidth}\centering\caption{الخريطة الثالثة}\label{11:fig:3}\end{subfigure}&
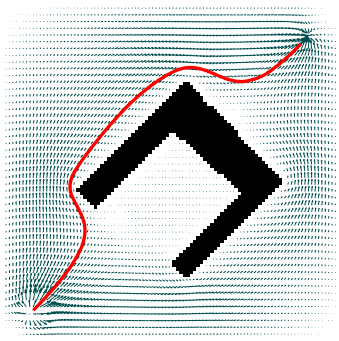
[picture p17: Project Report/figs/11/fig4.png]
		\begin{subfigure}{0.4\textwidth}\centering\caption{الخريطة الرابعة}\label{11:fig:4}\end{subfigure}\\
	\end{tabular}
	\caption{أداء الخوارزمية لعدة خرائط}
	\label{tab:mytable}
\end{table}
\end{center}

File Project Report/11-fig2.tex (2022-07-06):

	\begin{table}
		\centering
		\begin{tabular}{cp{150pt}}
			\begin{subfigure}{0.35\textwidth}
				\centering
				\includesvg[width=0.9\linewidth]{figs/11/fig5}
			\end{subfigure}&  انشاء مصفوفة بأبعاد الخريطة ياوضع عليها الروبوتات الباقية من السرب. أبعاد الروبوتات في المصفوفة يتناسب مع أبعاد الروبوت (المصفوفة $\mathcal{M}$) \\
			\begin{subfigure}{0.35\textwidth}
				\centering
				\includesvg[width=0.9\linewidth]{figs/11/fig6}
			\end{subfigure}& التحويل المسافي $D(\mathcal{M})$\\
			\begin{subfigure}{0.35\textwidth}
				\centering
				\includesvg[width=0.9\linewidth]{figs/11/fig7}
			\end{subfigure}&  $\mathcal{M}_2 = \epsilon (1/D(\mathcal{M}) - 1/k )^2$ \\
			\begin{subfigure}{0.35\textwidth}
				\centering
				\includesvg[width=0.9\linewidth]{figs/11/fig8}
			\end{subfigure}& $ \mathcal{M}_2 > k $ \\
			\begin{subfigure}{0.35\textwidth}
				\centering
				\includesvg[width=0.9\linewidth]{figs/11/fig9}
			\end{subfigure}& $ \nabla (\mathcal{M}_2 > k) $
		\end{tabular}
		\caption{عملية حساب المسار في الحالة الأولى من الحل}
		\label{11:fig:process}
	\end{table}

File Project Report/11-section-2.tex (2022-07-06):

أفضت الطريقة المتبعة في انتاج مسار لروبوت واحد في فضاء اختياري نتائج عالية الوثوقية والأمان، التجارب أثبتت بشكل كبير قدرة هذه الطريقة على إنتاج طريق ناعم حال وجود اتصال بين المبدأ والهدف. يعد تعميم هذه الطريقة لضمان وصول مجموعة روبوتات إلى هدفها عملية غاية في التعقيد، وذلك خصوصاً لطبيعة الروبوتات الغير هولنومية المدروسة في هذا المشروع. يمكن الاستدلال إلى تهجين بين عدة طرق لإيجاد ما يناسب حالات خاصة من فضاءات اعمل في الدراسات المرجعية.
لنتمكن من انتاج حل يتسم بالبساطة الاستدلالية وبالحتمية والكمالية، يجب العودة إلى الآلية التي تتصرف فيها جزيئات سائل وجدت نفسها في حقل كموني. إن ألية التفكير هذه تفضي إلى نوعين من الحلول:

\begin{itemize}
	\item الروبوتات غير واعية لبعضها
	\item الروبوتات (الجزيئات) واعية لبعضها
\end{itemize}

يمكن مقاربة الحل الأول بجزيئات سائل لا نيوتوني تسير في حقل السرعة المنتج، والطريقة الثانية بعدد من الأجسام صلبة تهوي في هذا الحقل.

\subsubsection{الروبوتات غير الواعية لوجود السرب}

هنا يتم احتساب حقل كموني صغير خارج من كل روبوت في السرب وإضافة هذه الحقول إلى حقل السرعة منهاً للتصادم، يتم هنا احتساب جميع قيم السرعة في كل نقاط الفضاء عن طريق أخذ جريان المائع من جهة والجيران من جهة أخرة. يمكن التحكم بقوة الحقل الكموني النافر الصادر عن كل روبوت بتغيير بارامترات الحساب.
ألية الحساب:

يتم أولاً ملء الخريطة فارغة بأجسام تتناسب أبعادها مع أبعاد الروبوتات الباقية في السرب، ثم يتم حساب تحويل المسافة للمصفوفة الناتجة \textenglish{(distance transform).} يتبع هذه الخطوة القيام بعملية مشروحة في الجدول \ref{11:fig:process}.

\input{11-fig2.tex}

ثم يتم جمع الحقل الناتج إلى حقول السرعة وإنتاج الحقل الخاص بكل روبوت. انزلاق الروبوت على الحقل الناتج يضمن وصوله إلى الهدف بسلاسة. انظر الشكل \ref{11:fig:square_map} كمثال.

\begin{figure}[htbp]
	\centering
	\includesvg[width=0.7\linewidth]{figs/11/square_map}
	\caption{مثال عن الطريقة المقترحة}
	\label{11:fig:square_map}
\end{figure}

\subsubsection{الروبوتات الواعية لوجود السرب}

يتم في هذه الطريقة برمجة وجود نابض ومخمد بين كل روبوتين متجاورين من روبوتات السرب. وجود هذه النظام الميكانيكي سيضمن حركة السرب ضمن تشكيلة معينة نجمية تحدد عناصرها من بارامترات البرمجة. يمكن حساب القوة المتبادلة بين روبوتين متجاورين كالتالي:

\begin{equation}
F_{ij}=F_k+F_c=k\left(d_{ij}-d_0\right)+c\frac{d}{dt}\left(d_{ij}-d_0\right)
\end{equation}
وبعدها يتم تحصيل القوى باستخدام:
\begin{equation}
\vec{\mathcal{F}_i}=\ \sum_{j\in\mathbb{N}_i}{\vec{F_{ij}}\ }
\end{equation}

تجمع القوة السابقة مع القوة الناتجة عن وجود حقل سرعة مائع لإنتاج خطوة المشي الجديدة. انظر الشكل \ref{11:fig:6}

\begin{figure}[htbp]
	\centering
	\includesvg[width=0.7\linewidth]{figs/11/fig61}
	\caption{القوى المتبادلة بين الروبوتات ممثلة كعناصر ميكانيكية}
	\label{11:fig:6}
\end{figure}

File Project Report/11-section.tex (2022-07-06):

\subsection{الخوارزمية المقترحة لروبوت واحد}

تعتمد الخوارزمية المقترحة لإنتاج طريق يسلكه الروبوت في بيئته على انشاء حقل سرعة يمكن للروبوت الانحدار فيه مشكلاً طريقه الخاص. نعتمد هنا على انشاء هذا الحقل عن طريق حل المعادلة التفاضلية الجزئية لتدفق السوائل الغير قابلة للانضغاط من نقطة الى أخرى.
أولاً، نكتب معادلات نافيير-ستوكس بشكلها المتجهي الخاصة بالموائع غير القابلة للانضغاط:

\begin{equation}
 \nabla \cdot \vec{\upsilon} = 0  
\end{equation}

\begin{equation}
 \frac{\partial \upsilon }{\partial t} +  \left(\vec{\upsilon }\cdot\nabla\right)\vec{\upsilon } = -\frac{1}{\rho}\nabla p+\nu\nabla^2\vec{\upsilon } 
\end{equation}

حيث $\vec{\upsilon } = (u,v,w)^T$ مركبات السرعة على المحاور الإحداثية الثلاث.

المعادلة الأولى تمثل انحفاظ الكتلة عند ثبات الكثافة (عدم الانضغاطية)، وتمثل المعادلة الثانية انحفاظ العزم. في الموائع غير الانضغاطية، معادلة انحفاظ الكتلة تخلق قيد كينيماتيكي يتطلب من حقل الضغط أن يتغير بشكل يسمح ل معدل تغير السرعة $\nabla \cdot \vec{\upsilon}$ بالانعدام في كل نقاط الفضاء. يمكن بناء حقل الضغط بأخذ تباعد (divergence) معادلة العزم، بعد أخد هذه الخطوة تظهر معادلة بواسون للضغط.

نعيد كتابة معادلات نافيير-ستوكس بشكل مريح للتقطيع وذلك بعد تعويض $ w=0 $:

\begin{equation}\label{eq:11:3}
\frac{\partial u}{\partial t}+u\frac{\partial u}{\partial x}+v\frac{\partial u}{\partial y}=-\frac{1}{\rho}\frac{\partial p}{\partial x}+\nu\left(\frac{\partial^2u}{\partial x^2}+\frac{\partial^2u}{\partial y^2}\right)
\end{equation}

\begin{equation}\label{eq:11:4}
\frac{\partial v}{\partial t}+u\frac{\partial v}{\partial x}+v\frac{\partial v}{\partial y}=-\frac{1}{\rho}\frac{\partial p}{\partial y}+\nu\left(\frac{\partial^2v}{\partial x^2}+\frac{\partial^2v}{\partial y^2}\right)
\end{equation}

\begin{equation}\label{eq:11:5}
\frac{\partial^2p}{\partial x^2}+\frac{\partial^2p}{\partial y^2}=-\rho\left(\frac{\partial u}{\partial x}\frac{\partial u}{\partial x}+2\frac{\partial u}{\partial y}\frac{\partial v}{\partial x}+\frac{\partial v}{\partial y}\frac{\partial v}{\partial y}\right)
\end{equation}

نتجه الآن لإنشاء mesh خاص بالمكان يسمح لنا بحل هذه المعادلات بيسر. اتجهنا لاستخدام تقطيع المكان الى مربعات لسهولة برمجتها. تظهر الصورة في الملحق رقم 1 تقطيع لحلبة مولدة عشوائياً. بعد تقطيع الحلبة يمكن بسهولة نقل \ref{eq:11:3} , \ref{eq:11:4} , \ref{eq:11:5} الى المتقطع بالشكل:

\begin{equation}
\begin{matrix}&\frac{u_{i,j}^{n+1}-u_{i,j}^n}{\Delta t}+u_{i,j}^n\frac{u_{i,j}^n-u_{i-1,j}^n}{\Delta x}+v_{i,j}^n\frac{u_{i,j}^n-u_{i,j-1}^n}{\Delta y}=\\&-\frac{1}{\rho}\frac{p_{i+1,j}^n-p_{i-1,j}^n}{2\Delta x}+\nu\left(\frac{u_{i+1,j}^n-2u_{i,j}^n+u_{i-1,j}^n}{\Delta x^2}+\frac{u_{i,j+1}^n-2u_{i,j}^n+u_{i,j-1}^n}{\Delta y^2}\right)\\\end{matrix}
\end{equation}

\begin{equation}
\begin{matrix}&\frac{v_{i,j}^{n+1}-v_{i,j}^n}{\Delta t}+u_{i,j}^n\frac{v_{i,j}^n-v_{i-1,j}^n}{\Delta x}+v_{i,j}^n\frac{v_{i,j}^n-v_{i,j-1}^n}{\Delta y}=\\&-\frac{1}{\rho}\frac{p_{i,j+1}^n-p_{i,j-1}^n}{2\Delta y}+\nu\left(\frac{v_{i+1,j}^n-2v_{i,j}^n+v_{i-1,j}^n}{\Delta x^2}+\frac{v_{i,j+1}^n-2v_{i,j}^n+v_{i,j-1}^n}{\Delta y^2}\right)\\\end{matrix}
\end{equation}

\begin{equation}
\begin{matrix}

\frac{p_{i+1,j}^n-2p_{i,j}^n+p_{i-1,j}^n}{\Delta x^2}+\frac{p_{i,j+1}^n-2p_{i,j}^n+p_{i,j-1}^n}{\Delta y^2} =

\\

\frac{\rho}{\Delta t}\left(\frac{u_{i+1,j}-u_{i-1,j}}{2\Delta x}+\frac{v_{i,j+1}-v_{i,j-1}}{2\Delta y}\right)-\frac{u_{i+1,j}-u_{i-1,j}}{2\Delta x}\frac{u_{i+1,j}-u_{i-1,j}}{2\Delta x} - 
\\
2\rho \frac{u_{i,j+1}-u_{i,j-1}}{2\Delta y}\frac{v_{i+1,j}-v_{i-1,j}}{2\Delta x}-\frac{v_{i,j+1}-v_{i,j-1}}{2\Delta y}\frac{v_{i,j+1}-v_{i,j-1}}{2\Delta y}

\end{matrix}
\end{equation}

بإعادة ترتيب المعادلات السابقة يمكن الحصول على الأطراف المتقدمة زمنياً:

\begin{equation}
\begin{matrix}u_{i,j}^{n+1}=u_{i,j}^n-u_{i,j}^n\frac{\Delta t}{\Delta x}(u_{i,j}^n-u_{i-1,j}^n)-v_{i,j}^n\frac{\Delta t}{\Delta y}(u_{i,j}^n-u_{i,j-1}^n)\\-\frac{\Delta t}{\rho2\Delta x}(p_{i+1,j}^n-p_{i-1,j}^n)\\+\nu\left(\frac{\Delta t}{\Delta x^2}\left(u_{i+1,j}^n-2u_{i,j}^n+u_{i-1,j}^n\right)+\frac{\Delta t}{\Delta y^2}\left(u_{i,j+1}^n-2u_{i,j}^n+u_{i,j-1}^n\right)\ \right)\\\end{matrix}
\end{equation}

\begin{equation}
\begin{matrix}v_{i,j}^{n+1}=v_{i,j}^n-u_{i,j}^n\frac{\Delta t}{\Delta x}\left(v_{i,j}^n-v_{i-1,j}^n\right)-v_{i,j}^n\frac{\Delta t}{\Delta y}\left(v_{i,j}^n-v_{i,j-1}^n\right)\ \ \\-\frac{\Delta t}{\rho2\Delta y}\left(p_{i,j+1}^n-p_{i,j-1}^n\right)\\+\nu\left(\frac{\Delta t}{\Delta x^2}\left(v_{i+1,j}^n-2v_{i,j}^n+v_{i-1,j}^n\right)+\frac{\Delta t}{\Delta y^2}\left(v_{i,j+1}^n-2v_{i,j}^n+v_{i,j-1}^n\right)\ \right)\\\end{matrix}
\end{equation}

\begin{equation}
\begin{matrix}
p_{i,j}^{n+1}=\frac{\left(p_{i+1,j}^n+p_{i-1,j}^n\right)\Delta y^2+\left(p_{i,j+1}^n+p_{i,j-1}^n\right)\Delta x^2}{2\left(\Delta x^2+\Delta y^2\right)}\ -\frac{\rho\Delta x^2\Delta y^2}{2\left(\Delta x^2+\Delta y^2\right)}
\\
\times\biggl[\frac{1}{\Delta t}\left(\frac{u_{i+1,j}-u_{i-1,j}}{2\Delta x}+\frac{v_{i,j+1}-v_{i,j-1}}{2\Delta y}\right)-\frac{u_{i+1,j}-u_{i-1,j}}{2\Delta x}\frac{u_{i+1,j}-u_{i-1,j}}{2\Delta x}\\-2\frac{u_{i,j+1}-u_{i,j-1}}{2\Delta y}\frac{v_{i+1,j}-v_{i-1,j}}{2\Delta x}-\frac{v_{i,j+1}-v_{i,j-1}}{2\Delta y}\frac{v_{i,j+1}-v_{i,j-1}}{2\Delta y}\biggr]

\end{matrix}
\end{equation}

\subsubsection{شروط المسألة: }
\begin{itemize}
	\item السرعة الابتدائية والضغط الابتدائي معدومان.
	\item السرعة معدومة عند الجدران .
	\item مشتق الضغط المكاني معدوم عند الجدران.
	\item الضغط +a عند نقطة انطلاق الروبوت -a عند الهدف.
	\item الضغط صفر عند الجدران.
\end{itemize}

بالحل الرقمي الـiterative يمكن الحصول على الحالة الثابتة steady state للمائع بعد عدد معين من التكرارات حيث يتم حساب السرعات المتقدمة بزمن قدره $\Delta t$. يمكن اختبار الوصول الى الحالة الثابتة من عدمه عن طريق معاينة $ \frac{dv}{dt}\ ,\frac{du}{dt} $ في كل iteration وانهاء الحساب عند هبوطه عن حد معين $ \epsilon $. عند الحصول على الحل النهائي نقوم بجعل الروبوت ينحدر باستخدام الحقل المتجهي الناتج موصلاً نفسه الى الهدف بشكل مباشر.
عند انشاء حقل السرعة لخريطة بأبعاد $ 100\times100  $ يستغرق الحاسوب الموصوف في ما متوسطه 500 ميلي ثانية. نذكر هنا أن هذا الزمن لا يعبر عن أصغر زمن يمكن للنظام انتاج حقل به، فهو لم يتعرض لأمثلة من هذه النواحي بعد:
\begin{itemize}
	\item شكل التقطيع.
	\item المعاملات الفيزيائية للمائع.
	\item التسريع باستخدام العتاد الصلب \textenglish{(Hardware Acceleration)}.
	
\end{itemize}

نوضح فيما يلي أمثلة عن حل الخوارزمية لعدة فضاءات عمل:
\input{11-fig1.tex}

\subsection{الخوارزمية المقترحة للسرب}

\input{11-section-2.tex}

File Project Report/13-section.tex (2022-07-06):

النموذج الديناميكي للروبوت التفاضلي مدروس بشكل كامل مع استنتاجه في أغلب الكتب النصية الخاصة بأساسيات علم الروبوت. نكتفي هنا بإدراج معالة$  \dot{\mathbb{S}\ } $

\begin{equation}
\dot{\mathbb{S}}=\left(\begin{matrix}\dot{x}\\\dot{y}\\\dot{\theta}\\\end{matrix}\right)=\left(\begin{matrix}\frac{\left(u_1+u_2\right)}{2}\cos {\theta}\\\frac{\left(u_1+u_2\right)}{2}\sin{\theta}\\\frac{\left(u_1-u_2\right)}{l}\\\end{matrix}\right)
\end{equation}

حيث يمثل $ u_1 $, $ u_2 $ السرعة الخطية للعجلات، و$ l $ المسافة بين العجلتين.

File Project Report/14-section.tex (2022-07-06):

تخدم العجلات وظيفتين رئيسيتين: الأولى هي دورها الأساسي لتحريك الروبوت، والثانية هي كأقراص مشققة لتسجيل حركة المحركات. نناقش في هذا القسم الأدوات الرياضية والشروط التصميمية الموافقة لما سبق.
العجلات للحركة
عند اجراء التجارب المخبرية على سرعات المحركات الموجودة متبوعة بعلب سرعتها، وجدنا أن السرعة عند $ 7.5 V $ (أي السرعة الأعظمية) كانت $ 135 $ دورة في الدقيقة. عند وضع شرط أن الروبوت يجب أن يكون قادر على قطع الحلبة شاقولياً أو افقياً خلال مدة أقصاها عشر ثوان، وجدنا أن السرعة الخطية يجب أن تكون أكبر من $ 0.24\ m.s^{-1} $. هذا جعل من السهل حساب أن نصف قطر الدولاب المطلوب يجب أن يكون أكبر من $ 1.7E-2\ m.  $. ان اختيار نصف قطر الدولاب أيضاً يخضع أيضاً لقيد آخر هو شقوق مسجلات الحركة.

\subsubsection{العجلات كمسجلات حركة}

من المعلوم أنه لإنشاء نظام تحكم دقيق يجب وجود نظام تحسس للزاوية وسرعة حركة المحركات. أول طريقة وأكثرها شيوعاً هي استخدام قرص مشقق بفتحات ذات ابعاد متساوية. يقوم مقطع ضوئي بمقاطعة المتحكم عند تسجيل مرور فتحة أمامه مما يسمح للمتحكم بتسجيل عبور هذه الفتحة، مما يؤدي لتسجيل تغير في الزاوية مقداره الزاوية المصممة بين الفتحتين$  \vartheta $.

\begin{equation}
	\vartheta=\frac{2\pi}{n}
\end{equation}

حيث يمثل n عدد الفتحات الموجودة على القرص. نعرف $ \phi $ بأنها الزاوية التي يمسحها المقطع الضوئي لعبور شق واحد. ومنه يمكن تعريف $ \eta=\frac{\phi}{\vartheta}$ ، وهي نسبة عرض الشق الى مجمل الزاوية $ \vartheta $. يمكن مضاعفة الدقة عن طريق جعل وحدة المقاطعة الخارجية الموجودة في المتحكم AVR تقوم بتسجيل الحافة الصاعدة والهابطة في إشارة المقطع. فتصبح $  \Delta d $ (أصغر مسافة يمكن للمسجل قراءتها):

\begin{equation}
\Delta d=\frac{\vartheta}{2}r=\ \frac{\pi}{n}r
\end{equation}

يسمح وجود مقطع ضوئي واحد بتسجيل تغيرات الزاوية دون معرفة اتجاه الدوران. لقراءة اتجاه الدوران يجب إضافة مقطع ضوئي ثان متموضع مع فرق طور مقداره $ \vartheta/4  $ بالنسبة للمقطع الأول. ان تحريك المقطع الضوئي الثاني بعدد صحيح من مضاعفات $ \vartheta $ لن يغير من أداء عمله، لكن سيمكن المصمم من وضع كلا الحساسين في مكان مريح للفك والتركيب السريعين، مما يتوافق مع أحد أهم شروط الهيكل الخارجي للروبوت. نسمي المسافة بين الحساسين $  \psi $، ونعتبر أن الحساس الأول موضوع في المبدأ. 

بنقل هذه الشروط الى معادلات رياضية:

\begin{equation}
\vartheta=\frac{2\pi}{n}
\end{equation}

\begin{equation}
	\rightarrow\psi=\frac{\vartheta}{4}+{k}\vartheta=\left(\frac{\eta}{2}+{k}\right)\vartheta
\end{equation}

حيث $ {k}\in\mathbb{Z} $. إذا وضعنا شروط التالية:

\begin{itemize}
	\item دقة تسجيل الحركة يجب أن تكون أصغر من الدقة التي نستطيع الحصول عليها من الكاميرا.
	\item 	الزاوية بين المقطعين ($ \psi $) يجب أن تكون بين $ \frac{\pi}{4} $ و $ \frac{3\pi}{4} $.
	\item 	الزاوية بين المقطعين يجب أن تكون عدد صحيح من مضاعفات $ \frac{\pi}{180}\times5 $ لتسهيل عملية التصميم.
	\item 	عرض الشق لا يقل عن $1.2 E-3m$.
\end{itemize}

تولد الشروط مسألة البرمجة الصحيحة الآتية:

إيجاد $k, \eta, n, r$ حيث:
\begin{equation}
\psi=\frac{\phi}{2}+\mathcal{k}\vartheta=\left(\frac{\eta}{2}+\mathcal{k}\right)\vartheta
\end{equation}
\begin{equation}
\Delta d<2.5E-3\rightarrow\frac{r}{n}<2\times3.979E-4
\end{equation}
\begin{equation}
\psi=\mathcal{q}\ \left(\frac{\pi}{180}\times5\right),\ where\ \mathcal{q}\in\mathbb{Z}
\end{equation}
\begin{equation}
\frac{\pi}{4}\le\psi\le\frac{3\pi}{4}
\end{equation}

تسمى المسألة السابقة بأنها مسألة برمجة صحيحة بسبب وجود شرط انتماء $k$ الى مجموعة الأعداد الصحيحة. تم اثبات ان مسائل البرمجة الصحيحة هي مسائل NP-Hard ويحتاج حلها الى استخدام احدى تقنيات البحث مع القليل من الأمثلة. لن نتطرق الى استخدام هذه الطرق بسبب قلة عدد القيود على المسألة وصغر فضاء الحل، اذ يمكن عبور كل مجال الحل وتسجيل أفضل نقطة.

بعد حل المسألة السابقة يمكن استخلاص ما يلي:
\begin{equation}
\eta=0.5
\end{equation}
\begin{equation}
r=2E-2\ m
\end{equation}
\begin{equation}
\psi=210\times\frac{\pi}{180}\ rad
\end{equation}
\begin{equation}
n=33
\end{equation}
\begin{equation}
\Delta d=1.9E-3\ m
\end{equation}
ومنه ينتج تصميم العجل الموضح في الشّكل \ref{14:fig:1}.

\begin{figure}[htbp]
	\centering
	\includesvg[width=0.7\linewidth]{figs/14/fig1}
	\caption{تصميم عجلات الروبوت الناتج}
	\label{14:fig:1}
\end{figure}

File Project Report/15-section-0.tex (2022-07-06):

تتألف منصة العمل من: 1) فضاء عمل و2) الروبوتات. يشرح هذا الفصل الأسس الرياضية والمعايير المتبعة في تصميم ما سبق. نبدأ بشرح فضاء العمل والشروط التصميمية التي يفرضها على تصميم الروبوتات، ثم ننتقل الى عرض تصميم الروبوتات بشقيه الرياضي والحاسوبي.

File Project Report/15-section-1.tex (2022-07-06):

يعرف فضاء عمل أي نظام روبوتي بمجموعة النقاط التي يستطيع الروبوت التواجد فيها بشكل آمن. نذكر هنا أن فضاء العمل لا يكون بالضرورة معرف بأساس الاحداثيات المكانية، على سبيل المثال، يمكن تعريف فضاء عمل ذراع روبوت بدلالة قيم مفاصل هذه الذراع، ويكون عدد أبعاده بعدد درجات حرية الذراع. يستخدم فضاء العمل بشكل أساسي للبحث عن مسارات يستطيع الروبوت عبورها بغية انجاز عمل معين. قد يكون هذا العمل غير مقيد، كإيجاد مسار بين موضع الروبوت الحالي ونقطة هدف محددة مسبقاً، وقد يكون مقيد بشروط معينة كإيجاد أقصر مسار أو أقلها استهلاكاً للطاقة. يمكّننا التعريف الجيد لفضاء العمل من إيجاد قيود المسألة التي يحاول الروبوت حلها بغية إيجاز المهمة الموكلة له، بمعنى أكثر دقة، تشكيل فضاء العمل هو أول خطوة من حل مسألة تخطيط المسار، التي تعتبر مسألة أمثلة.
يبين الشكل \ref{15:fig:4} فضاء عمل سرب الروبوتات. يتكون من مربع بضلع 2.4 متر وحواف مرتفعة. يحتوي المربع على عدة عوائق بأشكال مكعب أو أسطوانة وبأبعاد مختلفة. يمكن للعوائق أن تتحرك بالشكل المطلوب على الشبكة لتشكيل فضاء عمل ديناميكي.
 
 \begin{figure}[h]
 	\centering
 	
 	\caption{ إخراج ثلاثي الأبعاد لمنصة العمل}
 	\label{15:fig:4}
 \end{figure}

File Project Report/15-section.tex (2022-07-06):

\subsection{نظرة عامة}

\subsection{الأدوات}
\subsubsection{التغذية الراجعة}
إنّ تحديد نظام التّغذية الرّاجعة (XYTheta feedback) كان الخطوة الأساسيّة لنا لوضع تصوّر أساسي للمشروع ولبدء عمليّة التّصميم واختيار القطع الإلكترونيّة بحيث نحصل على أفضل أداء ممكن وفق تصميم مناسب وأسعار مقبولة. اعتمدنا في هذه المرحلة على نظام نقاط بين 1 و 5 - حيث يشير الرّقم 5 إلى الأفضليّة العليا – للمفاضلة بين الخيارات المتاحة وفق معايير محدّدة كما هو موضّح في الجدول أدناه.

\begin{table}[h]
	\begin{tabular}{lccccccc|}
		\cline{2-8}
	\multicolumn{1}{l|}{} & الحاجة للاختبار  &  فعالية التحكم & سهولة التطبيق & سهولة التصميم  & الحاجة  & السعر &    \\ \hline
		\multicolumn{1}{|l}{Dead Reckoner} & 3 & 4 & 4 & 5 & 3 & 5 & 24 \\ \hline
		\multicolumn{1}{|l}{Mouse Sensor}  & 1 & 5 & 2 & 3 & 5 & 4 & 20 \\ \hline
		\multicolumn{1}{|l}{Camera}        & 5 & 5 & 2 & 5 & 3 & 5 & 25 \\ \hline
	\end{tabular}
\end{table}

بعد عمليّة المقارنة وبناءً على النّتائج الموضّحة أعلاه كان خيار استخراج مواقع الرّوبوتات من كاميرا مثبّتة فوق حلبة عمل الرّوبوتات هو الخيار الأفضل. 
أمّا عمليّة اختيار الكاميرا فكانت ترتكز على معيارين أساسين وهما الحصول على تغطية كاملة للمنّصة و عدد الأطر التي يمكن الحصول عليها في الثّانية الواحدة. لذلك قمنا باختيار كاميرا ستريو واسعة الزّاوية الّتي تعدّ خياراً مناسبا لنا. حيث أنّ  أبعاد حساس كل كاميرا 960×2560 بكسل. يمكن بسهولة إيجاد أنّ أصغر مسافة يمكن قياسها باستخدام الكاميرا عن طريق تقسيم عرض فضاء العمل ( على دقة حسّاس الكاميرا و النتيجة هي 2.5 mm. بالإضافة إلى إمكانيّة الحصول على 16 إطار بالثّانية وهو تردّد كافٍ لمتابعة سير الروبوتات وتحديد مواقعها.

\subsubsection{المحرك}
المعايير الأساسيّة الّتي تمّ اعتمادها لاختيار المحركات: طريقة قياس لموضع وطريقة قيادة الرّوبوت ولقد اعتمدنا لتحديد ذلك النّظام النّقطي السّابق الّذي اعتمدناه لتحديد نظام التّغذية الرّاجعة في الفقرة السّابقة.

\begin{table}[h]
	\begin{tabular}{lccccccc|}
		\cline{2-8}
		\multicolumn{1}{l|}{} & الحاجة للاختبار  &  فعالية التحكم & سهولة التطبيق & سهولة التصميم  & الحاجة  & السعر &    \\ \hline
		\multicolumn{1}{|l}{ODD BLDC} & 1 & 5 & 1 & 1 & 3 & 4 & 15 \\ \hline
		\multicolumn{1}{|l}{Micro Servo}  & 5 & 3 & 5 & 5 & 3 & 1 & 22 \\ \hline
		\multicolumn{1}{|l}{Gear DC}        & 2 & 4 & 1 & 1 & 2 & 3 & 13 \\ \hline
	\end{tabular}
\end{table}

كما نرى في الجدول السّابق فإنّ محرّك الـ Micro servo كان الخيار الأكثر ملائمة ولاسيّما مع سهولة استخدامه وتغليفه الّذي سوف يسهّل عمليّة التّصميم بشكل كبير  بالإضافة إلى سعره المقبول. ولكنّه كان بحاجة لعمليّة اختبار للتأكد من مدى قدرتنا على التّحكم به و عن مدى قدرتنا على التّحكم به. لذلك قمنا باالتّجريب على محرك SG90 Continuous 360 Degree. يبلغ وزن المحرك 9 غرام وعزمه عند جهد تغذية 4.8 فولت $1.3 Kg.cm$ وسرعة الدوران الأعظمية 110 دورة في الدقيقة.

لكنّ نتائج الاختبار لم تكن مرضية بشكل كامل؛ حيث بينت الاختبارات وجود منطقة ميتة في خرج الاكودر الداخلي للمحرك dead band. لكنّ الخيارات الاخرى كانت غير مناسبة من ناحية التّوافر؛ لذلك لجأنا إلى حل آخر، وهو فصل محرّك التّيار المستمرّ الموجود داخل الـ SG90  عن دارة قيادته ووصله مع المقاومة المتغيّرة الدّاخلية إلى دراتنا السفليّة و باالتّالي يمكن استخدام محرّكات تيّار مستمرّ بحجم مناسب وضمن تغليف مناسب مّما سهّل علينا عمليّة تصميم الجسم وتصغير حجمه بالإضافة إلى السّعر المناسب. كما أنّنا سوف نقوم باستخدام العجلات كمسجلّات للحركة من أجل تحكّم أكثر دقّة.

\subsubsection*{قيادة المحرك}
 بالنّسبة لقيادة محركات التيار المستمر، فتم ذلك باستخدام الجسر L298. يعاني الجسر من عدة مشاكل أهمها قدم تكنولوجيا TTL المستخدمة في صناعته، وأيضاً كبر حجمه. ممّا فرض قيوداً في الحجم والشّكل على تصميم الدّارات  لذلك استخدمنا L298N - Dual Full-Bridge Driver IC وسنرى لاحقا كيف أنّ تصميم الدّارات وتجميعها مكّننا من تنفيذ الشروط المطلوبة للتّصميم ضمن القيود المفروضة عليه.
 
\subsection{وحدة التحكم}
لتغطية كافة احتياجات النظام الإلكتروني تمّ وضع عدة نقاط رئيسية يجب على النظام المدمج في الروبوت شملها:

\begin{itemize}
	\item اتصال آمن وبتأخير (latency) منخفضة بين الروبوت والنظام المركزي.
	\item القدرة على قيادة محركي DC بجهد أعظمي 7.5 v وتيار 0.5 A أعظمي.
	\item عرض نبضة بتردد متوافق من الثابت الزمني للمحرك.
	\item نظام تحديد سرعة وموضع كل من محركي التيار المستمر.
	\item نظام تغذية.
	\item وحدات ادخال وإخراج بدائية بغية الـdebugging وتبديل البارامترات الداخلية on-the-run.
\end{itemize}

اعتمدنا على سلسلة متحكمات الـ 8 bit الخاصة بشركة Atmel ذات الـInstruction set RISC. يوجد في هذه المتحكمات 35 تعليمة بالإضافة لعدة وحدات توقيت ومقاطعات داخلية وخارجية تجعل المهمة المطلوبة ممكنة. ولقد اخترنا المتحكّم  Atmega328p tqfp.

يمتلك المتحكم Atmega328p المواصفات الآتية:
\begin{english}
\begin{itemize}
	\item Two 8-bit Timer/Counter
	\item One 16-bit Timer/Counter
	\item UART Connection Unit
	\item Two External Interrupt Unit
	\item I2C Unit
	\item Three 8-bit I/O units
	\item One ADC Unit with MUX to 8-bit I/O Unit
\end{itemize}
\end{english}

يضمن وجود ثلاث مؤقتات/عدادات قدرة النظام على جدولة المهام حسب أولوياتها وحسب الوقت المطلوب لها. كما انها توفر العتاد المطلوب لتشكيل إشارة بعرض نبضة متغير PWM تستخدم لقيادة محركات التيار المستمر. (يتم تشكيلها باستخدام الـHardware). توفر وحدة الـUART الاتصال المباشر بين وحدة الاتصال وبين المتحكم وبشكل سهل ومباشر وآمن من الأخطاء. أما بالنسبة للمقاطعات الخارجية: فهي تسمح للمتحكم بتسجيل الحركة التي تسجلها المقاطعات الضوئية المستخدمة في قراءة دوران المحرك.

\subsection{التغذية}

باختلاف التّصورات المحتملة لسرب الرّوبوتات، فإنّ كل روبوت ضمن السّرب يحتاج إلى إمداده بطاقة لإكمال المهمّة الموكلة له. ولقد قمنا باختيار بطّاريات  Lithium-Ion القابلة لإعادة الشّحن؛ حيث يمكن إعادة شحن هذا النّوع من البّطاريات مئات المرّات مع الحفاظ على ثباتها وأدائها مقارنةً بغيرها من البطّاريات. تميل بطّاريات Lithium-Ion إلى أن تكون ذات كثافة طاقة أعلى، معدّل تفريغ ذاتي أقلّ من البطّاريات الأخرى القابلة لإعادة الشّحن؛ ممّا يؤدّي إلى تحسين كفاءة الطاقة حيث تتمتّع الخليّة الواحدة باحتفاظ بالشّحن لفترة أطول من أنواع البطّاريات الأخرى. أمّا بالنّسبة للشكل: فلقد اخترنا بطاريات بأبعاد ( 4 mm× 4 cm ×5 cm ) لكي تتناسب مع التّصميم. وتقدّم هذه البطّاريات جهداً مقداره 3.7 V وتتوضّع عليها دارة حماية.

إنّ استخدام مصدر تغذية قابل لإعادة الشّحن يفرض علينا استخدام وحدة شحن وتفريغ. ولقد استخدمنا وحدات TP4056A المستخدمة لشحن وتفريغ بطّاريات اللّيثوم أيّون. ونظراً إلى أنّ البطّاريّات المستخدمة تقدّم جهد 3.7 V؛ احتجنا إلى استخدام وحدة رافع جهد (DC- DC convertor). إنّ دخل دارة رافع الجهد يتراوح بين 3 إلى 15 فولت، بينما يكون الخرج من 4 إلى 35 فولت، ويتمّ ضبطها لإعطاء الخرج المطلوب بشكل يدوي.

\subsection{نظام الاتصال}
بعد قراءة الدّراسات المرجعيّة واستشارة المختصّين تم اعتماد تقنية الواي فاي لربط الروبوتات مع بعضها ومع الحاسوب المركزي. ولاختيار وحدة الواي فاي المناسبة.
% Please add the following required packages to your document preamble:
% \usepackage{multirow}
\begin{table}[h]
	\resizebox{\textwidth}{!}{\begin{tabular}{lrccccc|}
			\cline{3-7}
			\multicolumn{2}{l}{\multirow{2}{*}{}}                                                                                                               & \multicolumn{2}{|c|}{\textbf{وحدات   بدائية}}       & \multicolumn{3}{c|}{\textbf{وحدات   مطوّرة}}                                \\ \cline{3-7} 
			\multicolumn{2}{l}{}                                                                                                                                & \multicolumn{1}{|c}{ESP-01}              & ESP-12e             & NodeMcu-DevKit-V1.0 & NodeMcu-Lua-WIFI-Board & Wemos-D1-Mini       \\ \hline
			\multicolumn{1}{|l|}{المداخل   والمخارج للأغراض العامّة} & GPIO & 2                   & 11                  & 11                  & 11                     & 11                  \\ \hline
			\multicolumn{1}{|l|}{محوّل   تماثلي رقمي}                & ADC       & -                   & 1                   & 1                   & 1                      & 1                   \\ \hline
			\multicolumn{1}{|l|}{هوائي}                              & Antenna                                                                                  & مطبوعة   على الدارة & مطبوعة   على الدارة & مطبوعة   على الدارة & مطبوعة   على الدارة    & مطبوعة   على الدارة \\ \hline
			\multicolumn{1}{|l|}{إمكانيّة   الوصل المباشر}           & USB-to-Serial                                                                            & غير ممكن            & غير ممكن            & ممكن                & ممكن                   & ممكن                \\ \hline
			\multicolumn{1}{|l|}{عامل   الشّكل}                      & Form                                                                              & صغير                & متوسط               & كبير                & كبير                   & متوسط               \\ \hline
			\multicolumn{1}{|l|}{وحدة الـ  ESP8266}                  & ESP8266 Module                                                                           & -                   & -                   & ESP12E & ESP12E   & ESP12E       \\ \hline
			\multicolumn{1}{|l|}{شريحة   الوصل المباشر}              & Serial                                                                              & -                   & -                   & CH340G              & CP2102                 & CH340G              \\ \hline
			\multicolumn{1}{|l|}{غطاء لحجب   التّرددات الرّاديويّة}  & RF-shield                                                                             & لايوجد              & يوجد                & يوجد                & يوجد                   & يوجد                \\ \hline
	\end{tabular}}
	\label{table::rfmodule}
	\caption{جدول مقارنة بين وحدات الاتصال المختلفة}
\end{table}

وتم التقييم وفق معايير معينة وهي الوثوقية، الحجم، التوافرية، السعر، وامكانية الوصل المباشر (USB-to-Serial) . بناءً على هذه المعايير والجدول السّابق قمنا باختيار وحدة الاتّصال Wemos  ؛ حيث أنّها تحقق ذات وثثوقيّة عالية مقارنة بسعرها وحجمها مناسب بالإضافة إلى توافرها.

\subsection{الدارة الالكترونية المطبوعة PCB}

يتم قيادة محرك التيار المستمر باستخدام الجسر L298. يعاني الجسر من عدة مشاكل أهمها قدم تكنولوجيا TTL المستخدمة في صناعته، وأيضاً كبر حجمه. ممّا فرض قيوداً في الحجم والشّكل على تصميم الدّارات. سوف نعرض في الفقرتين التاليتين تجميعة الدارات التي مكنتنا من تنفيذ الشروط السابقة ضمن قيود الحجم والشكل المفروضة عليه. حيث سنقوم في القسم الأول بشرح عملية تصميم أمّا في القسم الثّاني سوف نقوم باستعراض عمليّة التّصنيع.

\subsubsection{التصميم باستخدام الحاسب}
لقد استخدمنا البرنامج التّصميمي Altium لتصميم الطّبقة العلويّة والسفليّة. حيث أن الطّبقة العلويّة تحتوي على وحدة الاتصال والمتحكّم الصغري ووحدات الادخال والإخراج، بينما يحتوي يضم القسم السّفلي جسر القيادة، وحدات التغذية وشحن المدخرة، ودارات المقطعات الضوئية. 

\subsubsection*{الطبقة العلوية:  طبقة المعالجة والإشارة}
 هذه الطبقة مسؤولة عن أي اجراء على الروبوت القيام به حسابياً أو لتلقي أوامر الحركة من حاسوب مركزي. تحوي الطبقة متحكمين اثنين: الأول بمعمارية RISC AVR 8 bit والثاني 32-bit. يوفر المعالج الأول الوسائل المنطقية والتوقيتية للتحكم بالمحركات بدقة وكذلك لإجراء حسابات المعادلات الفروقية بدور تقطيع بالغ الدقة، أي للقيادة منخفضة المستوى. أما المتحكم الثاني فيوفر آلية اتصال ببروتوكول Wi-Fi بين روبوتات السرب وبين القاعدة، وكذلك بعض الحسابات عالية المستوى كتقطيع المسار وموائمة التراسل بين الروبوت والحاسوب المركزي وملاحقة حركة الروبوت. يوجد المنتج النهائي للدارة في الشكل \ref{15:fig:1}
 
 \subsubsection*{الطبقة السفلية: طبقة التضخيم والإشارة}
 إن العزل الحاصل بين كل من التضخيم والاشارة يضمن إمكانية ملاحقة الأخطاء وعزل السبب ان كان كهربائي أو الكتروني-برمجي. تضمن هذه الطبقة تحسس ومراقبة كل من موضع وتيار المحركات باستخدام مفاهيم كهربائية بسيطة، وكذلك توفر إمكانية الربط الكهربائي بين كل من دارتي الشحن ورفع الجهد من جهة، وبين المدخرة من جهة ثانية.
 ان استخدام الجسر L298 لم يكن الخيار الأنسب كهربائياً، خصوصاً مع هذا الحمل المنخفض نسبياً. لكن عدم توفر بديل مناسب ضمن شروط الحجم الموضوعة مسبقاً جعله الخيار السليم. يوجد على الدارة أيضاً ديودات حماية كون المحرك المستخدم من النوع المستمر. لمراجعة الملفات التصميمية انظر الشكل \ref{15:fig:1}
 
 \begin{figure}[htbp]
 	\centering
 	\includesvg[width=0.85\linewidth]{figs/15/fig15_1}
 	\caption{التصميم باستخدام الحاسب لكل من الطبقتين العلوية والسفلية}
 	\label{15:fig:1}
 \end{figure}

\subsection{عملية تصنيع الدارات}

بعد عمليّة تصميم الدّارات انتقلنا إلى مرحلة التّصنيع، حيث أنّ كل طبقة (السفليّة والعلويّة) عبارة عن دارة ثنائيّة الجوانب أي كلّ أنّ منهما تتألّف من طبقتي نحاس مطليتين بمادة الفايبر غلاس (FR4)بسماكة$ 1.8 mm$.  ليأتي بعد ذلك غطاء اللّحام وهي الّتي تمنح الدّارة لونها الأرجوانيّ (أو أيّ لون آخر)، حيث يتمّ وضع هذه الطّبقة على طبقة النّحاس لعزل المسارات النّحاسيّة من الاتّصال الغير مقصود مع أيّ معدن أو لحام أو أطراف موصلة أخرى وهذه الطّبقة تساعد في وضع اللّحام في مكانه الصّحيح وتجنّب اللّحام الخاطئ ممّا سهّل عمليّة لحام القطع الإلكترونيّة السّطحيّة (SMD).  يلي طبقة غطاء اللّحام طبقة بيضاء من الحرير تدعى الشّاشة الحريريّة $ (Silk screen) $، وتستخدم هذه الطّبقة في إضافة الأحرف والرّموز والأرقام إلى ألواح الـ PCB ممّا يسهّل عمليّة تجميع المكوّنات على الألواح وفهمها بشكل أفضل.  يوضّح الشّكل أدناه الدّارات بعد عمليّة التّصنيع.

\begin{figure}[h]
	\centering
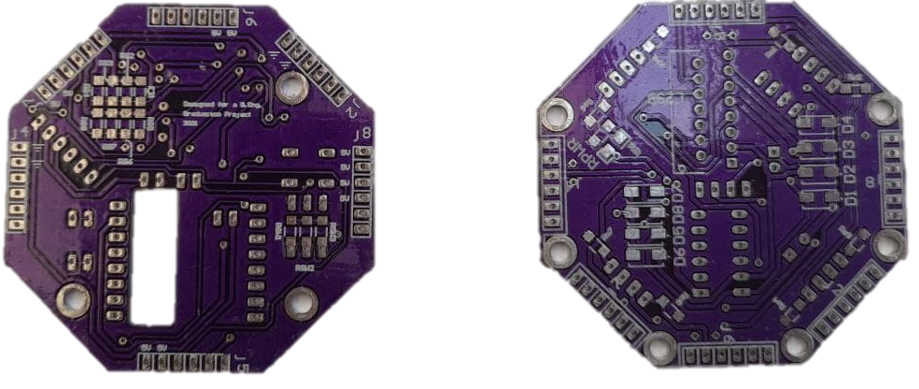
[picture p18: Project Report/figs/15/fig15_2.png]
	
	\caption{المنتج النهائي بعد تصنيع الدارة}
	\label{15:fig:2}
\end{figure}

\subsection{اختبار المنتج}

بعد عمليّة التّصنيع قمنا بعمليّة فحص للدّارات للتأكّد من التّوصيلات باستخدام الأدوات المختلفة. ووجدنا بعد عمليّة الفحص الأوليّة حدوث قصر في الدّارة ناتج عن انقطاع في الأرضي نتيجة القص الزّائد عند الأطراف، حيث أن أرضي الدّارة يتواجد في الأطراف والصّورة أدناه توضّح منطقة حدوث الانقطاع.

\begin{figure}[h]
	\centering
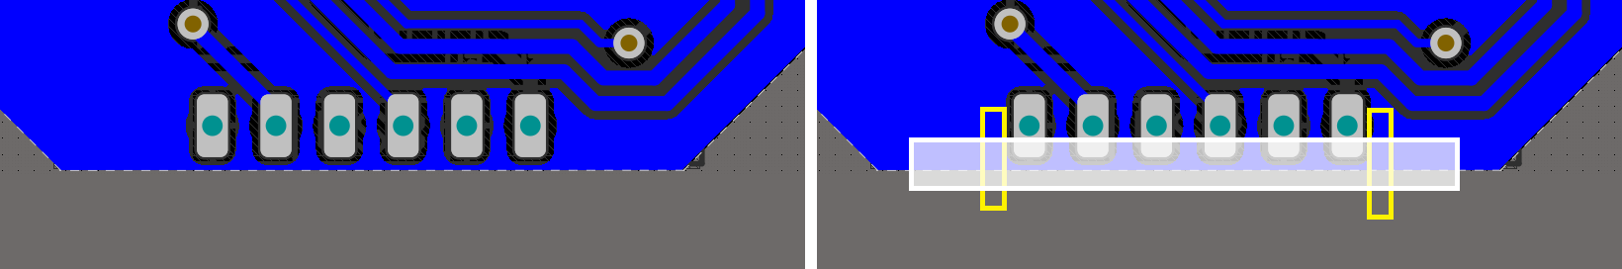
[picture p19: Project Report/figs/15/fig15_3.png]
	
	\caption{العطب الناتج عن التصنيع}
	\label{15:fig:3}
\end{figure}

لم يقتصر حدوث الانقطاع على منطقة الأرضي بل كان هناك انقطاعات في المناطق الموصلة عند الانتقال من جزء واسع إلى جزء ضيّق ($ necks $). بعد ذلك قمنا بإحصاء أماكن حدوث هذه المشكلة ووجدنا وجود انقطاعين في الطّبقة السّفليّة وانقطاعين في الطّبقة العليا وقمنا بوصل جميع المناطق المقطوعة بأسلاك خارجيّة.

\subsection{الجسم الخارجي والتحريك}

تم تصميم جسم الروبوت باستخدام برنامج SoildWorks واعتماد تصميم بسيط صغير الحجم بأبعاد 6×7×6 بشكل مثمن. تُثبت البطارية من الجهة السفلية للجسم ويوجد أماكن مخصصة لتثبيت المحركات والعجلات والمقاطعات الضوئية وتُبت الدراتين فوق الجسم باستخدام أربع براغي. كما هو موضح في الشكل 

 \begin{figure}[htbp]
	\centering
	\includesvg[width=0.85\linewidth]{figs/15/fig15_5}
	\caption{ الهيكل الخارجي للروبوت}
	\label{15:fig:5}
\end{figure}

تم تصنيع الجسم باستخدام تقنية الطباعة ثلاثية الأبعاد من مادة  Polylactic Acid (PLA)مع خصائص طباعة تتلخص في ارتفاع الطبقة 0.16 ملم وسماكة الجدران 0.8 ملم. 
بعد تجريب ثلاث ورشات متوفرة وسهلة الوصول جغرافيا، توصلنا إلى أفضل طباعة بشكل يضمن الجودة المطلوبة ولاسيما في تصنيع العجلات حيث أن أي اختلاف أو عدم انتظام في الثقوب سيؤثر مباشرة على قيم التغذية الراجعة التي سيعتمدها الروبوت لتتبع المسار الناتج. توضح الصورة \ref{15:fig:6} مقارنة بين علجة مثالية وعجلة ذات جودة تصنيع منخفضة.

\begin{figure}[h]
	\centering
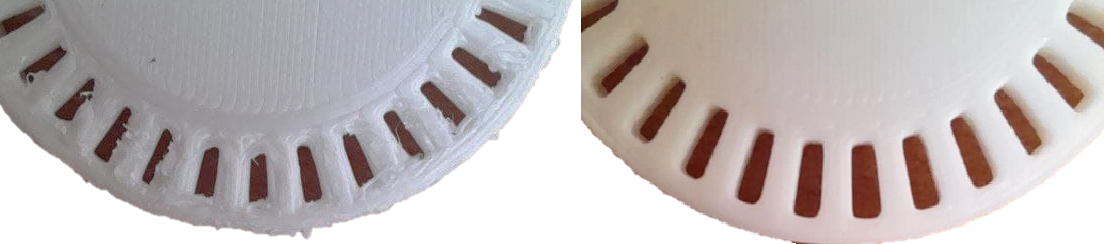
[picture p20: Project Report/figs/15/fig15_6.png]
	
	\caption{ مثال يوضح مقارنة بين سوء وجودة تصنيع العجلات}
	\label{15:fig:6}
\end{figure}

لضمان حركة مستقرة للروبوت على الأرض ونظراً لخفة وزن الروبوت، قمنا باختيار مادة مناسبة من الكاوتشوك لإحاطة إطارات كل العجلات و زيادة الاحتكاك وبعد التجريب تم تحقيق الغاية المرجوة حيث أن انزلاق العجلات على الأرض كان شبه معدوم. سنعرض النتائج النهائية لتركيب الروبوتات في فصل النتائج.

بالنّسبة لدور العجلات كمسجّلات حركة فكان يجب اختبار دقّة الطّباعة ثلاثيّة الأبعاد في إخراج الشّقوق الموجودة على العجلات، ولاختبار ذلك قمنا بتحريك العجلات بأقصى سرعة يمكن للروبوت السّير بها فكانت استجابة المقاطعات الضّوئيّة لعبور الشقوق عبرها كالتالي (الشكل \ref{15:fig:enc}): 

 \begin{figure}[htbp]
	\centering
	\includesvg[width=0.85\linewidth]{figs/15/fig_enc}
	\caption{استجابة المقاطعات الضّوئيّة}
	\label{15:fig:enc}
\end{figure}

\begin{figure}
	\centering
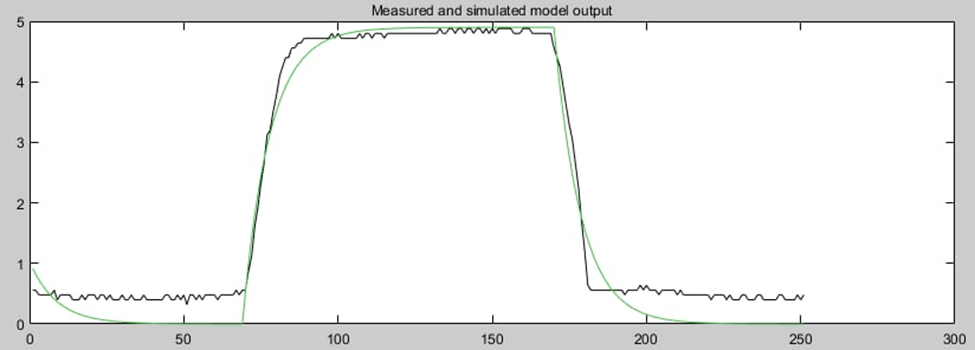
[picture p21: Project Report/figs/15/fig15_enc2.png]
	
	\caption{التقريب إلى نظام درجة أولى}
	\label{fig:fig15enc2}
\end{figure}

أمّا الخطوة التّالية فكانت اختبار استجابة الـ AVR للمقاطعات الضّوئيّة، وكما نلاحظ من قراءة الاستجابة الموضّحة في الشّكل \ref{fig:fig15enc3} وجود تاخير بسيط في استجابة الـ AVR.

\begin{figure}
	\centering
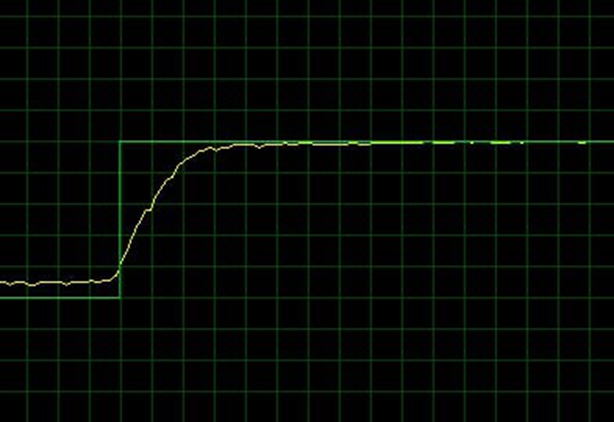
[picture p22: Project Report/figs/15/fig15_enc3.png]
	
	\caption{محاكاةاستجابة الـ AVR للمقاطعة الضّوئيّة}
	\label{fig:fig15enc3}
\end{figure}

ولتحسين قراءة المقاطعات الضّوئيّة قمنا بتصميم encoder وتصنيعه للحصول على حواف شقوق حادّة ومن ثمّ إطباقه على شقوق العجلات للحصول على أفضل استجابة ممكنة.

\begin{figure}
	\centering
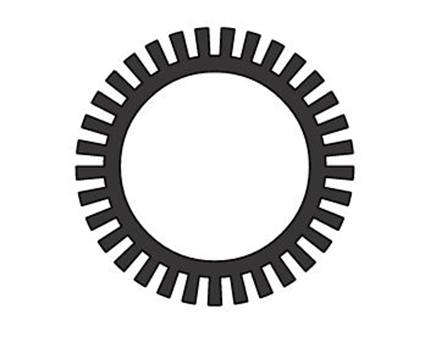
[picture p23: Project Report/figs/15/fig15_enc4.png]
	
	\caption{طبقة بلاستيكية لتحسن قراءة المقطعات}
	\label{fig:fig15enc4}
\end{figure}

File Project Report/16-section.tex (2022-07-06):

\subsection{نظام الاتصال}
\subsubsection{طوبولوجيا الشبكة}
على مستوى طبقة الـ Data Link، فلدينا العديد من الخيارات المُتاحة. قمنا في البداية بالعمل على بروتوكول ESP-NOW المُطوّر من قبل Espressif، وإنّ الاتّصال اعتماداً على هذا البروتوكول هو اتّصال موثوق TCP من دون الحاجة إلى عمليّات المُصافحة.
نظراً لأهميّة موثوقيّة الاتّصال فقد قمنا باختبار البروتوكول ESP-NOW (one to many) على خمس عقد، حيث تكون أحد العقد هي الـ Master والبقيّة Slaves كما هو موضّح في الشّكل \ref{fig:fig161}.
\begin{figure}
	\centering
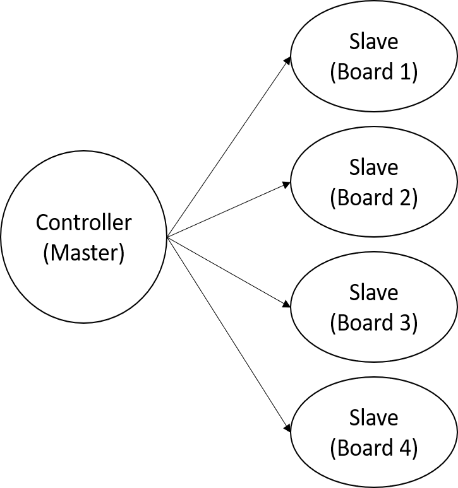
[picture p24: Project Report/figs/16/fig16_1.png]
	
	\caption{}
	\label{fig:fig161}
\end{figure}

يث قمنا في البداية بتعريف عنوان الـ MAC الخاص بكلّ شريحة اتّصال، ومن ثمّ إرسال إحداثيين x و y مولّدين عشوائياً لجميع العقد ألف مرّة وإعادة التّجربة من أجل أزمنة تأخير مُختلفة كما هو موضّح في الشّكل \ref{fig:fig162}، حيث يمثّل المحور الأفقي أزمن التأخير من أجل الشّرائح  الأربعة، أمّا المحور الشّاقولي فهو عبارة عن الرّسائل الألف المرسلة مُرتّبة من الرسالة الأولى في الأسفل إلى الرسالة الأخيرة في الأعلى.  يُعبّر اللّون الأحمر عن وصول الرّسالة فيما يشير الأسود إلى فشل تسليم الرّسالة.

\begin{figure}
	\centering
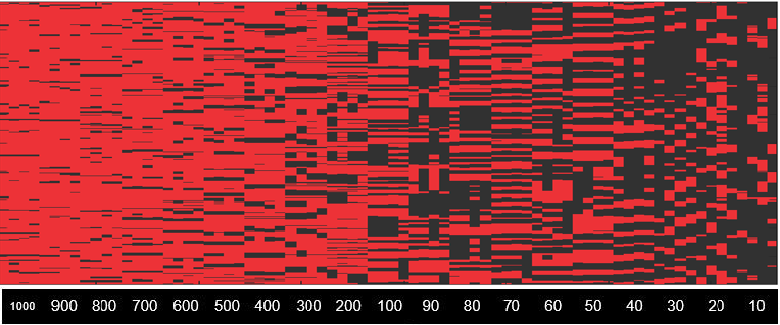
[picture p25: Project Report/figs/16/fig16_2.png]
	
	\caption{}
	\label{fig:fig162}
\end{figure}

\subsection{بروتوكول $ MQTT $}

هو بروتوكول نقل رسائل بين مخدّم زبون Client/Server بنمط نشر/اشتراك publish/subscribe قائم على الموضوع (Topic)؛ لأنّها ذات تطبيق مستقرّ للـ ESP8266  (باستخدام مخدّم Mosquitto MQTT) حسب [18]. وهنا يجب التّنويه لوجود ثلاث أنماط أساسيّة الاشتراك: النمط القائم على الموضوع والنمط القائم على المحتوى والنمط القائم على النوع.

إنّ بروتوكول MQTT (الموضح في الشكل \ref{fig:fig163}) يتكوّن من ثلاث أجزاء أساسيّة: المخدّم، النّاشر، والمشترك. يُعدّ المخدّم مسؤولاً عن إدارة شبكة من العملاء والّذين هم عبارة عن مزيج من النّاشرين والمشتركين؛ حيث أن النّاشر هو الجهاز الّذي يقوم بإرسال الرّسائل إلى المخدّم بحيث تكون هذه الرّسائل معنونة بعنوان موضوع (topic) بينما المشترك هو الجهاز الّذي يستمع لموضوع أو مواضيع معيّنة. يُمكن تشبيه الموضوع بوسم خاصّ بكلّ رسالة، ويمكن أن يكون وحيد الطّبقة أو متعدّد الطّبقات ويسمح هذا بتقسيم منطقي جيّد للمعطيات. على كلّ جهاز يرغب باستقبال موضوع معين أن يشترك به وذلك بإخبار المخدّم.
\begin{figure}
	\centering
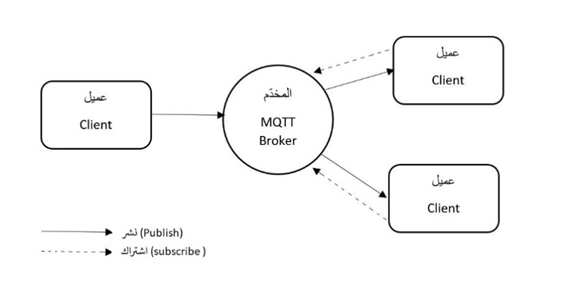
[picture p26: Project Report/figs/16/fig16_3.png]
	
	\caption{شكل توضيحي للأجزاء الأساسيّة في بروتوكول نقل الرّسائل MQTT}
	\label{fig:fig163}
\end{figure}

ليس هناك اتّصال مباشر بين المشترك والنّاشر وإنّما وببساطة يقوم المشترك بإخبار المخدّم أنّه مهتمّ بمواضيع محدّدة وبعد ذلك يقوم المخدّم بإرسال الرّسائل إلى المشتركين عند توافرها. إنّ نمط نشر/اشتراك مختلف تماماً عن نمط طلب/ردّ (request/response) المتّبع في بروتوكول الـ HTTP. كما أنّ بروتوكول الـ MQTT يعمل بالاعتماد على TCP/IP وعلى خلاف الـ HTTP فهو بروتوكول Binary وليس ASCII، وهذه إحدى ميّزاته فكما نعلم أنّ بروتوكولات الـ binary تستهلك كميّة نقل بيانات أقلّ من الشّبكة. بالإضافة إلى ذلك فهناك خيارات في بروتكول الـ MQTT تتعلّق بتوصيل الرّسالة بين المخدّم والعميل يُطلق عليها QoS (Quality of Service)، وهناك ثلاث خيارات بخصوص هذا الشّأن:

\begin{itemize}
	\item مستوى 0 (QoS = 0): توصيل الرّسالة مرّة واحدة في أفضل حالة؛ أيّ أنّه في حال لم يستلم المشترك الرّسالة فإنّ المُخدّم لن يقوم بإرسالها مرّة أخرى حيث لا يتوقّع المخدّم من المشترك تأكيد وصول الرّسالة (Acknowledgment).
	
	\item مستوى 1 (QoS = 1): توصيل الرّسالة مرّة واحد على الأقلّ. هذا يعني أنّ المخدّم يستمرّ بإرسال الرّسالة إلى أن يقوم المشترك باستلام الرّسالة ويرسل تأكيد باستلامها، وهذا يؤدّي إلى إمكانية وصول أكثر من رسالة واحدة إلى نفس المشترك.
	
	\item مستوى 2 (QoS=2): توصيل الرّسالة مرّة واحدة لزوماً، وهذا يعني أنّ الرّسالة يجب أن تصل لمرّة واحدة ودون تكرار المشترك.
	
\end{itemize}

وفي حال عدم اتّصال المشترك أساساً فيمكننا ضبط الإعدادات بحيث يبدأ الاتّصال بجلسة اتّصال نظيفة؛ حيث يقوم المُخدّم بتجاهل الرّسائل القديمة ويبدأ جلسة جديدة. بينما في حال تعطيل هذه الخاصيّة فإنّ الرسائل (من المستويين 0 و1) الّتي تمّ إرسالها إلى أحد المشتركين أثناء انقطاعه عن الشّبكة سوف تتراكم وسيقوم المُخدّم بإرسالها له فور اتّصاله بالشّبكة.

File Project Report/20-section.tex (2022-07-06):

كما أشرنا سابقاً فإنّ عمليّة التّحكم مركزيّة؛ حيث يوجد نظام تشغيل ROS على الحاسوب المركزي. يوجد على نظام ROS ثلاث عقد أساسيّة.
العقدة الأولى : تتصل مع الكاميرا المثبّتة أعلى المنصّة، حيث تقوم الكاميرا بإرسال الأطر لها لتقوم باستخلاص معلومات عن الخريطة ومواقع الرّوبوتات. ولتحقيق القراءة الدقيقة لمواقع الروبوتات في الزمن الحقيقي على الحاسوب المركزي سنعتمد مكتبة ArUco وهي مكتبة تستخدم في تطبيقات الواقع المعزز وتعتمد على مكتبة OpenCV  وتساعد في عملية معايرة الكاميرا. سيتم تثبيت علامات QR-markers على الروبوتات ومنه تقوم عقدة ال ArUCo في ال ROS تقوم باكتشاف وتحديد موقع العلامات وترسلها لل ROS-TOPIC .

\begin{figure}
	\centering
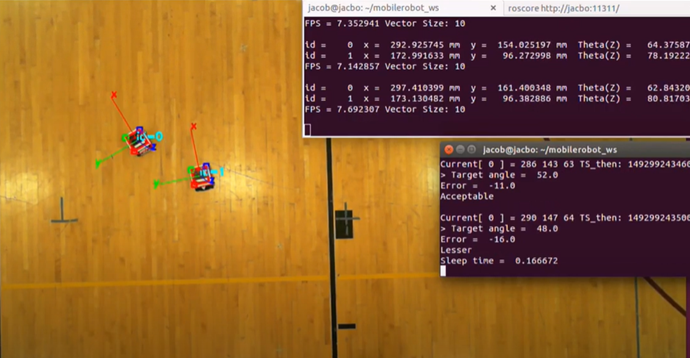
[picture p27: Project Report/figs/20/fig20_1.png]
	
	\caption{صورة توضيحيّة لآليّة عمل محددات ArUco}
	\label{20:fig:1}
\end{figure}

العقدة الثّانية: تقوم هذه العقدة باستقبال إحداثيّات الرّوبوتات والعوائق من العقدة الأولى عن طريق اشتراكها بالـ ROS TOPIC ذاته. بعد ذلك تتمّ على هذه العقدة عمليّة توليد المسار الأمثل وفق الخوارزميّة المختارة وإرسال نقاط المسارات الكاملة لجميع الرّوبوتات إلى العقدة الثّالقة.
العقدة الثّالثة: بعد استقبال هذه العقدة لنقاط المسارات الكاملة لجميع الرّوبوتات، تقوم بإرسال كلّ مسار إلى الـ Topic الخاص به  (إلى الرّوبوت الخاص به المشترك بنفس الـ Topic) عن طريق مخدّم الـ mqtt، لتكون هذه العقدة يمثابة عقدة وصل بين نظام ROS و مخدّم بروتوكول الـ mqtt.
وبعد أن يستقبل كلّ روبوت الرّسائل الخاصّة به تتكرّر هذه العمليّة بشكل دوري، ثمّ يقوم كلّ روبوت بتتيّع المسار وفق خوارزميّة تصحيح PID.

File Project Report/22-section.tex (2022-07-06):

كُتب برنامج تشغيل الروبوت باستخدام لغة c لقربها من العتاد الصلب ولدعمها من قبل منظومة GCC. كون المعالج بمعمارية 8 بت، هناك العديد من القيود على سرعة تنفيذ العمليات الحسابية عليه، فكلفة حساب متحول صحيح 32 بت أضعاف كلفة حساب ذات الرقم اذا كان مخزناً في متحول 8 بت. لا تواجه المعالجات الحاسوبية ذات معمارية 64 بت هذه المشاكل بشكل عام.

يمكن القول بأن نقطة الضعف الرئيسية لهذه المعالجات تكمن في عرض مسجلاتهاـ حيث تتميز بطيف واسع من المزايا المناسبة بشكل مطلق للتطبيق الحالي. 

صمم نظام تشغيل الروبوت بطريقة البرمجة التابعية لخلو لغة c من الأغراض والصفوف. نجد في الملحق توصيف شامل لكل أجزاء الكود البرمجي.

يتبع الروبوت المسار الواصل إليه عن طريق مصحح متقطع PID. تتكون حلقة الحساب من مصححين: الأول يتحكم بسرعة المحركين لعدم المسافة بين مركز الروبوت والنقطة الهدف، والثاني يقوم بعدم الزاوية بي شعاع سرعة الروبوت والشعاع الواصل بين مركز الروبوت والنقطة الهدف. عمل هذين المصححين ينتج مسارات مناسبة بين النقاط المتتابعة.

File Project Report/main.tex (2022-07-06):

%!TEX TS-program = xelatex

\documentclass[10pt,a4paper]{book}
\usepackage[utf8]{inputenc}
%\usepackage[english]{babel}
\usepackage{amsmath}
\usepackage{amsfonts}
\usepackage{amssymb}
\usepackage{graphicx}
\usepackage{multirow}
\usepackage{svg}
\usepackage{url}
\usepackage{booktabs}
\usepackage{subcaption}
\usepackage{geometry} 
\usepackage{setspace}
\usepackage{pdfpages}
\usepackage{titlesec}

\usepackage{floatrow}

\usepackage{hyperref}

\usepackage{fontspec}
\usepackage{polyglossia}
\setmainlanguage[calendar=gregorian,numerals=maghrib]{arabic}
\setotherlanguage{english}
\setmainfont{Simplified Arabic}
%%% Coloring the comment as blue

\usepackage[linesnumbered,ruled,vlined]{algorithm2e}

\newfontfamily\englishfont{Times New Roman}

\newfontfamily\arabicfont[Script = Arabic]{Simplified Arabic} % Replace 'Simplified Arabic' with a font from your system
\begin{document}
	\setstretch{1.4}
	
	\includepdf[pages=-]{01-cover.pdf}
	
	\begin{english}
		\begin{center}
			\textbf{Abstract}
		\end{center}
		\input{01-abstract.tex}	
		\pagebreak
	\end{english}

	\section{موجز البحث}
	
	\input{03-section.tex}
	
	\tableofcontents

	\chapter{مقدمة البحث}
	
	\section{خلفية وأهداف البحث}
	\input{05-section.tex}
	\section{الدراسات المرجعية}
	\input{06-section.tex}
	
	\section{أهداف المشروع}
	\input{07-section.tex}
	
	\section{مخطط العمل}
	\input{08-section.tex}
	
	\section{مخطط الأطروحة}
	\input{09-section.tex}

	\chapter{الدراسة الرياضية والنمذجة}

	\section{تخطيط المسار لروبوت واحد باستخدام الطرق التقليدية}
	
	\input{10-section.tex}
	
	\section{تعميم الحل للأسراب}
	
	\input{10-section-2.tex}
	
	\section{تخطيط المسار عن طريق المعادلات التفاضلية الجزئية لحركة الموائع}
	
	\input{11-section.tex}
	
	\section{التغذية الراجعة لشعاع حالة الروبوتات}
	\input{12-section.tex}
	
	\section{النموذج الرياضي العام للروبوت}
	
	\input{13-section.tex}
	
	\section{دراسة العجلات}
	\input{14-section.tex}
	
	\chapter{بنية النظام الصلبة والبرمجية}
	
	\section{مقدمة}
	\input{15-section-0.tex}
	
	\section{فضاء العمل}
	\input{15-section-1.tex}
	
	\section{بنية النظام الصلبة}
	\input{15-section.tex}
	\input{16-section.tex}
	\section{بنية النظام البرمجية}
	
	\subsection{نظرة عامة}
	\input{20-section.tex}
	
	\subsection{البنية البرمجية للروبوت منخفضة المستوى}
	\input{22-section.tex}

	\chapter{النتائج}
	
	بعد برمجة كل طرق توليد المسار المذكورة في الملف سيتم إجراء ما تبقى من تجارب تفريقية خلال الاسبوع القادم، حسث يجب إجراء جميع التجارب في ظروف عمل أقرب إلى المثالية وتضمن التطابق بين التكرارات. 
	
	يتم حاليا تحضير النتائج لكتابة الدرستين التاليتين:
	
	\begin{itemize}
		\item الدراسة الأولى عن تصميم وتنفيذ منصة سرب روبوتات لأغراض بحثية
		\item الدراسة الثانية عن مقارنة بين طريقة تخطيط المسار المقترحة والطرق الشهيرة في الدراسات المرجعية باستخدام المنصة المنجزة
	\end{itemize}

	\bibliographystyle{vancouver}
	\begin{english}
		\bibliography{ref}
	\end{english}
	
	\listoffigures
	\listoftables
	\chapter{الملحقات}
	\section{AVR C Code Referece Manual}
	
	\input{00-avr_refman.tex}
	
\end{document}

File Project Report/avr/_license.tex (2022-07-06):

Redistribution and use in source and binary forms, with or without modification, are permitted provided that the following conditions are met\+:

\begin{DoxyEnumerate}
\item Redistributions of source code must retain the above copyright notice, this list of conditions and the following disclaimer.
\item Redistributions in binary form must reproduce the above copyright notice, this list of conditions and the following disclaimer in the documentation and/or other materials provided with the distribution.
\item The name of Atmel may not be used to endorse or promote products derived from this software without specific prior written permission.
\item This software may only be redistributed and used in connection with an Atmel microcontroller product.
\end{DoxyEnumerate}

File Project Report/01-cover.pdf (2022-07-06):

# جامعة ترشين

) أطروحة باكلوريوس(

### تصممي وتنفيذ خوارزمية ختطيط مسار حسابية لـرسب روبواتت اعامتدا عىل احلل الرمقي للمعادالت التفاضلية اجلزئية اخلاصة

### جبراين املوائع

### لكية الهندسة املياكنيكية والكهرابئي ة

### برانمج هندسة املياكترونيكس متزيي ن

### للم

### أسامء الطالب املنفذي ن

### صبا عي س ندى سلامن عدانن سعود

### إابرشا ف د. مثىن ال قبي ل د. عيس الغنا م

2021 /06

# Tishreen University

(Bachelor’s Thesis)

Design and Implementation of a computational motion planning algorithm based on fluid dynamics PDE for Robotic Swarms

## Faculty of Mech. and Elec. Engineering Program of Mechatronics For the Distinguished

## Prepared by:

Siba Issa | Nada Salman | Adnan Saood
| Supervised by
Mothanna Alkubeily, Ph.D. | | Issa AlGhannam, Ph.D.

2021 /06

Syrian Arab Republic
Tishreen University
Faculty of Mech. and Elec. Engineering
Program of Mechatronics
for Distinguished

امجلهورية العربية السوري ة جامعة ترشي ن
لكية الهندسة املياكنيكية والكهرابئي ة متزيي ن

للم
برانمج املياكترونيك

# تصميم وتنفيذ خوارزمية تخطيط مسار حسابية لـسرب روبوتات اعتماداً على الحل الرقمي للمعادالت التفـاضلية الجزئية الخاصة بجريان الموائع

## أعّده الطالب :

## صبا عيس، ندى سلامن، وعدان ن سعود

## إابرشاف : ادلكتور مثىن القبيل، ادلكتور عيس الغنام

## جامعة ترشين، الالذقية، سوراي

06.2021

Syrian Arab Republic
Tishreen University
Faculty of Mech. and Elec. Engineering
Program of Mechatronics
for Distinguished

امجلهورية العربية السوري ة جامعة ترشي ن
لكية الهندسة املياكنيكية والكهرابئي ة متزيي ن

للم
برانمج املياكترونيك

## Design and Implementation of a computational motion planning algorithm based on fluid dynamics PDE for Robotic Swarms

### Prepared by

### Siba Issa, Nada Salman, Adnan Saood

### Supervisor by

### Prof. Mothanna Alkubeily, Prof. Issa AlGhannam

at

### Tishreen University, Latakia, Syria

02.2021

We, the Exam committee, certify that we have read this project and that in our opinion it is fully adequate, in scope and quality, as a thesis for final project.

Exam committee:

### تصادق جلنة احلمك بعد قراءهتا ومناقش هتا ملرشوعالتخرج عىل أنه مالمئ من حيث النوعية وا لمهية ليكون حبثا

ملرشوع التخرج.

### أسامء جلنة احلمك:

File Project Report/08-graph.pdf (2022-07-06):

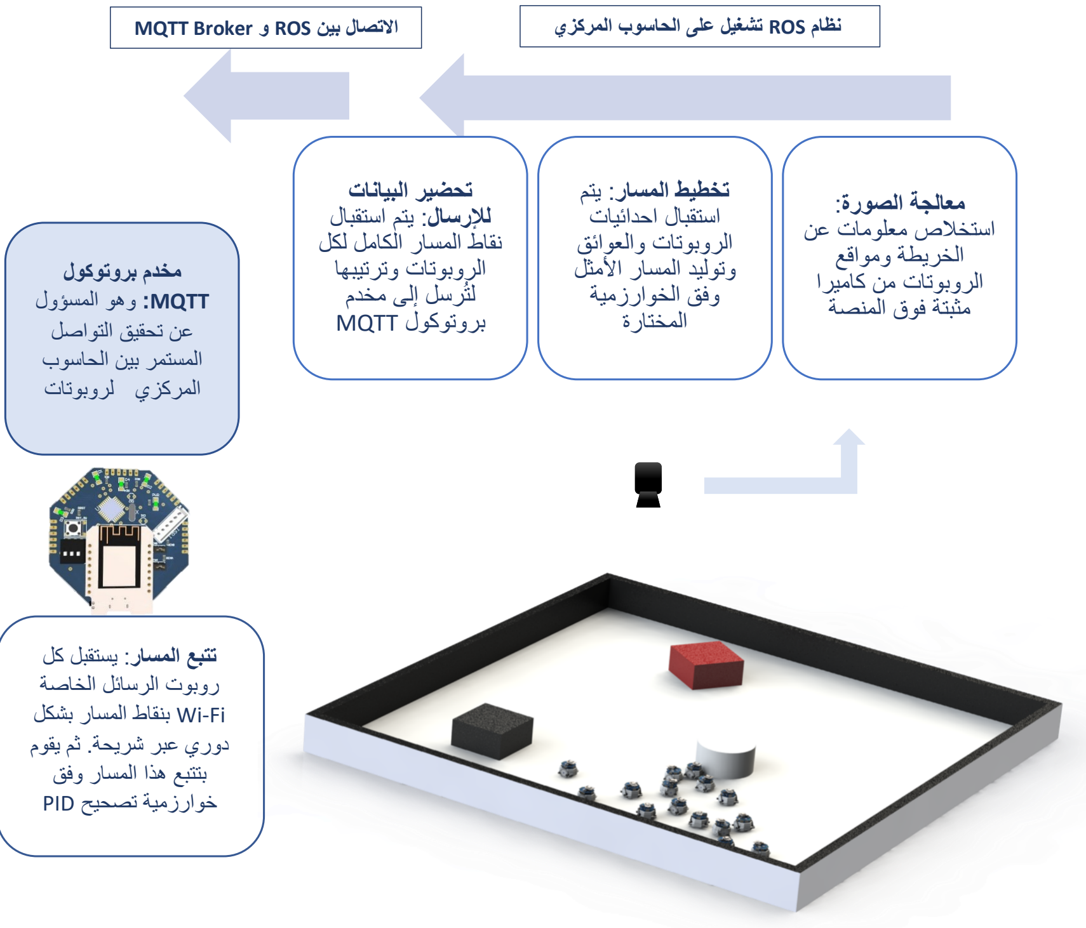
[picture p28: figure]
تحضير البيانات لإلرسال: يتم استقبال نقاط المسار الكامل لكل الروبوتات وترتيبها لتُرسل إلى مخدم بروتوكول MQTT; تخطيط المسار: يتم استقبال احدائيات الروبوتات والعوائق وتوليد المسار األمثل وفق الخوارزمية المختارة; معالجة الصورة: استخالص معلومات عن الخريطة ومواقع الروبوتات من كاميرا مثبتة فوق المنصة; مخدم بروتوكول MQTT: وهو المسؤول عن تحقيق التواصل المستمر بين الحاسوب المركزي والروبوتات; تتبع المسار: يستقبل كل روبوت الرسائل الخاصة Fi-Wi بنقاط المسار بشكل دوري عبر شريحة. ثم يقوم بتتبع هذا المسار وفق خوارزمية تصحيح PID

نظام ROS تشغيل على الحاسوب المركزي االتصال بين ROS و Broker MQTT

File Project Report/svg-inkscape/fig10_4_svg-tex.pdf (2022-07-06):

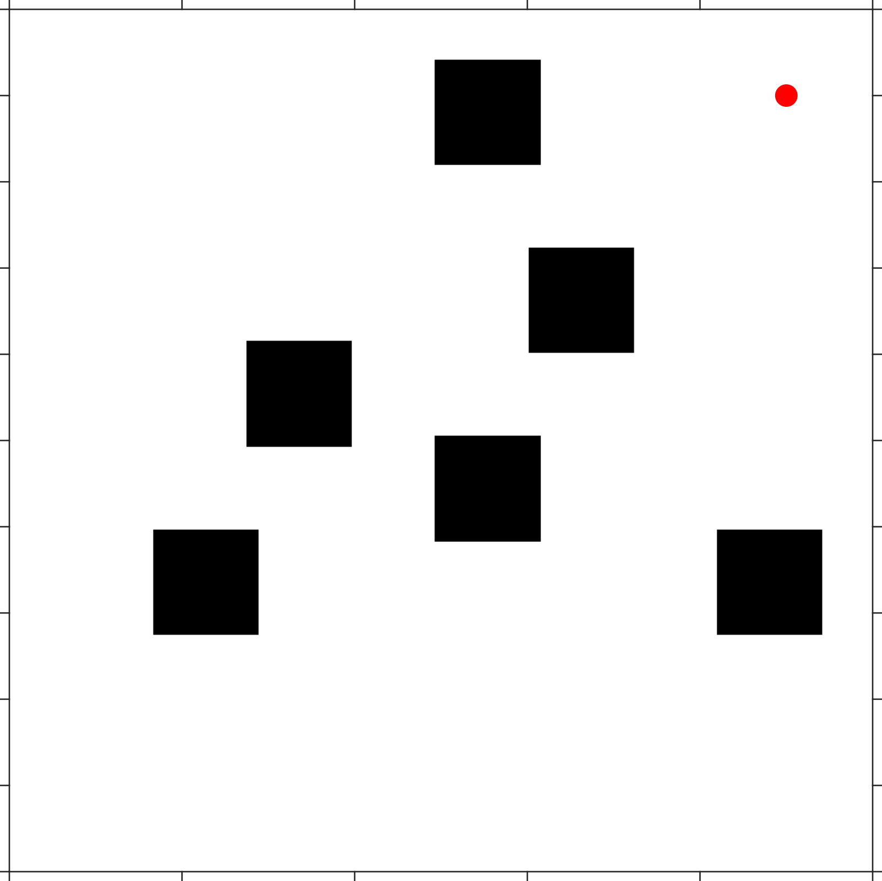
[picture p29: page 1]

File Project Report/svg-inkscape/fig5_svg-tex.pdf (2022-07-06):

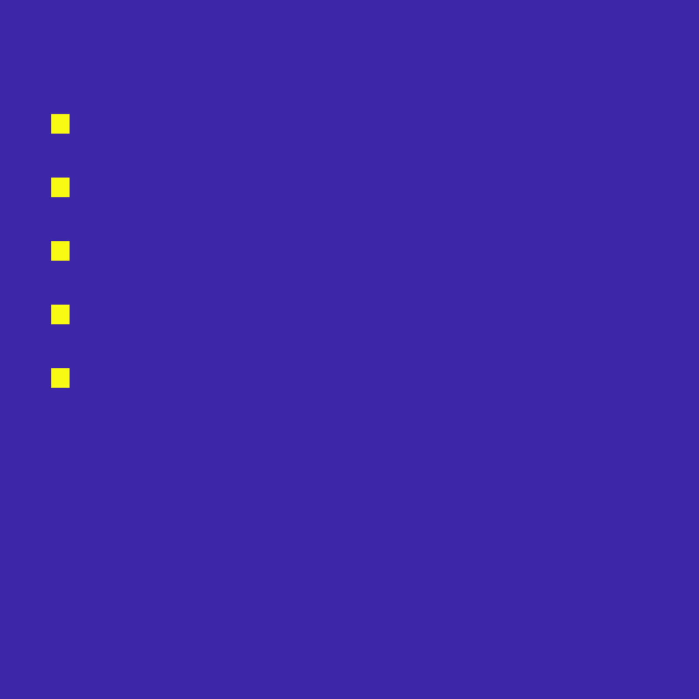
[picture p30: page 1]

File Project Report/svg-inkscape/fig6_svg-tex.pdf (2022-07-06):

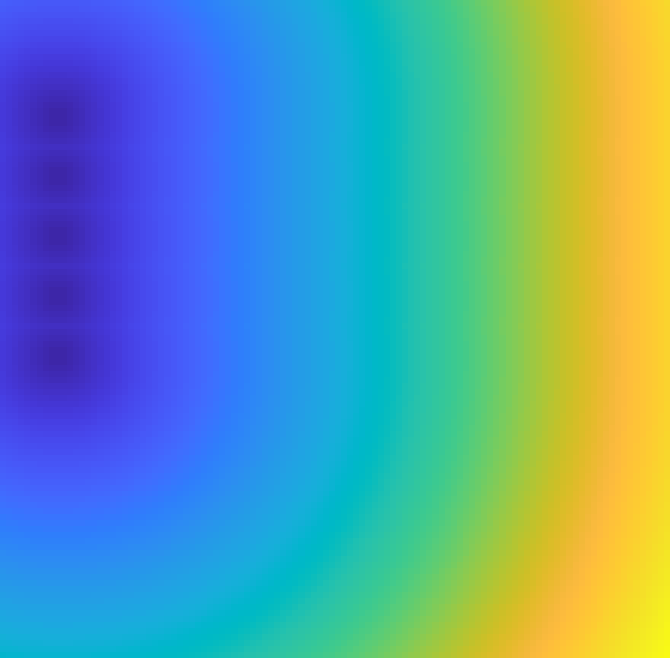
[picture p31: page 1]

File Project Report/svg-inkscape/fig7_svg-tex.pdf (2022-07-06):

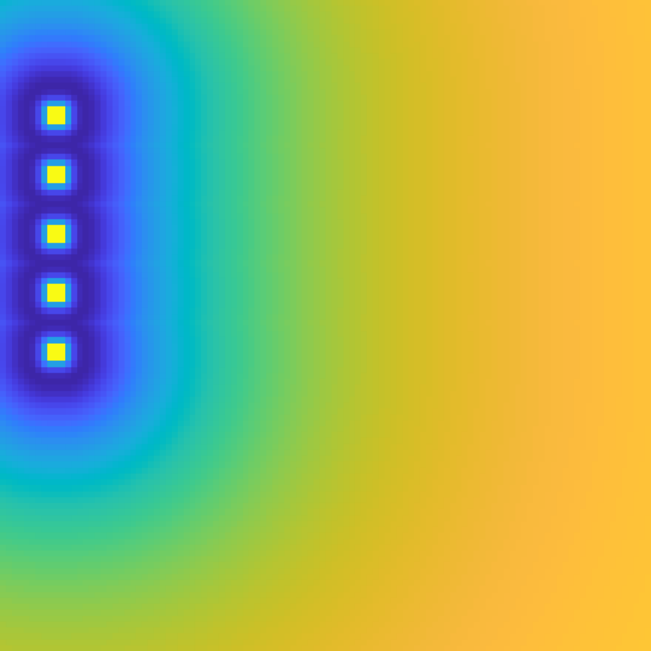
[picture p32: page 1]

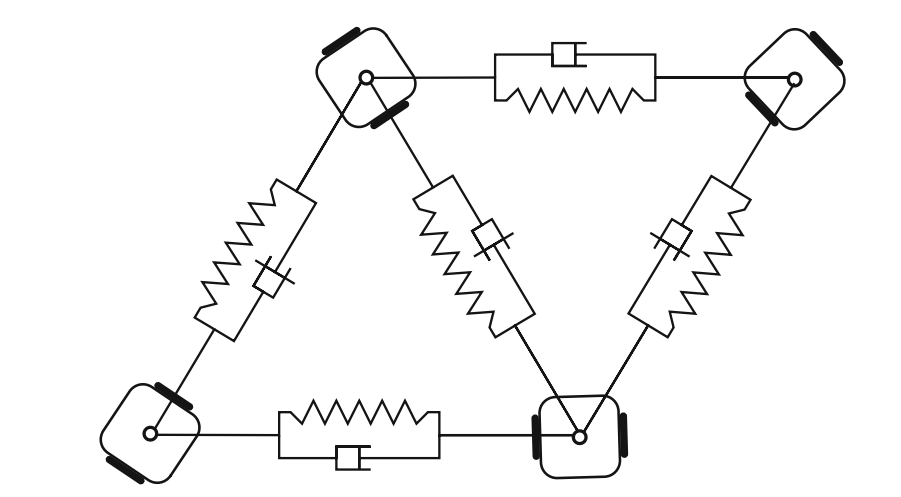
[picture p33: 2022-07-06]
Project Report/figs/11/Screenshot 2021-06-13 213356.png

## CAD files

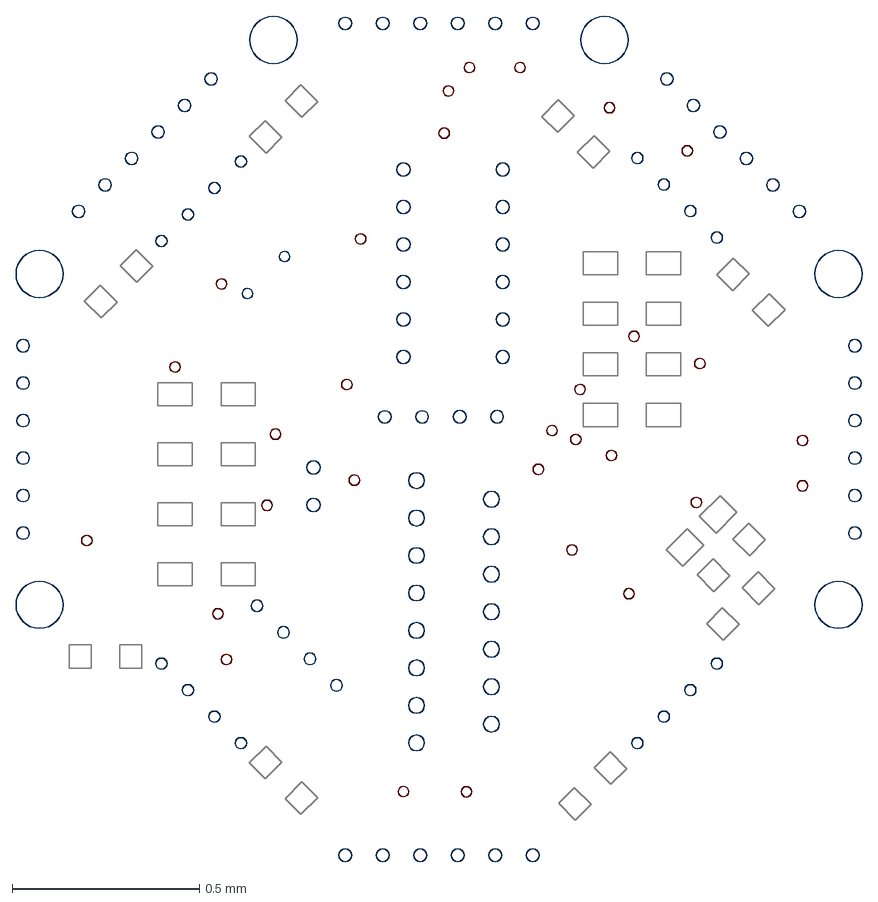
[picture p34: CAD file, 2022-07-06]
Circuits PCB Design/Bottom/stencil/main_btm.DXF
2.26 x 2.26 mm

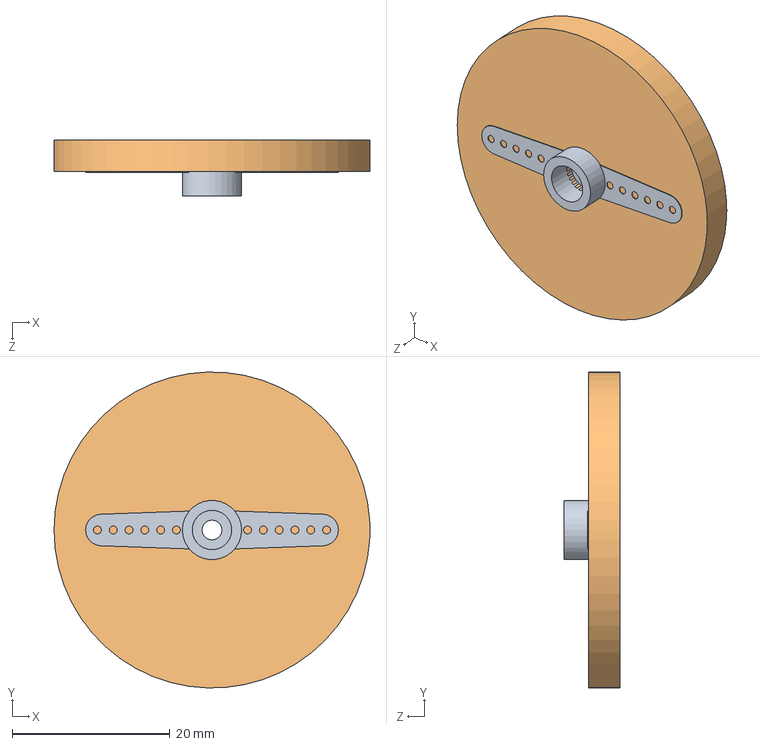
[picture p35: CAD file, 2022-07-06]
Body Design/temp.SLDASM
40.0 x 40.0 x 7.10 mm
Microservo horn
wheel40

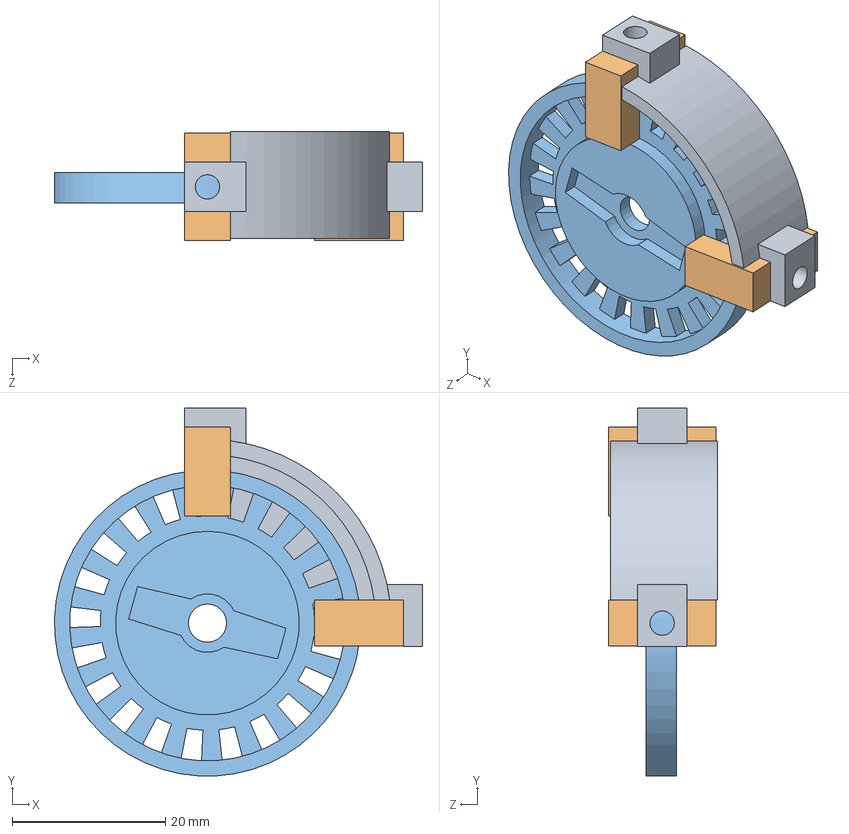
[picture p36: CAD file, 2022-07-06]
Body Design/wheel_w_encoder.SLDASM
48.1 x 48.1 x 14.3 mm
encoders_holder2
photo_interrupter x 2
wheel40

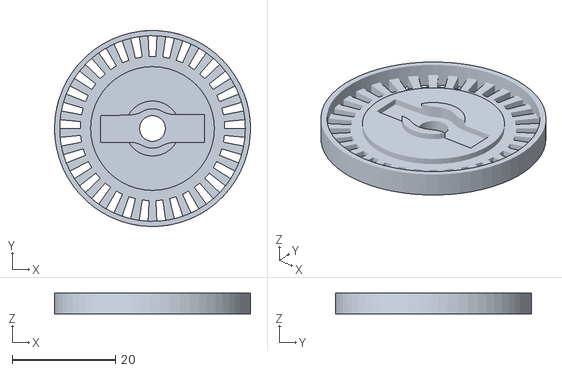
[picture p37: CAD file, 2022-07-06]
Body Design/3dprint/ver3/wheel38.STL
38.0 x 38.0 x 4.00

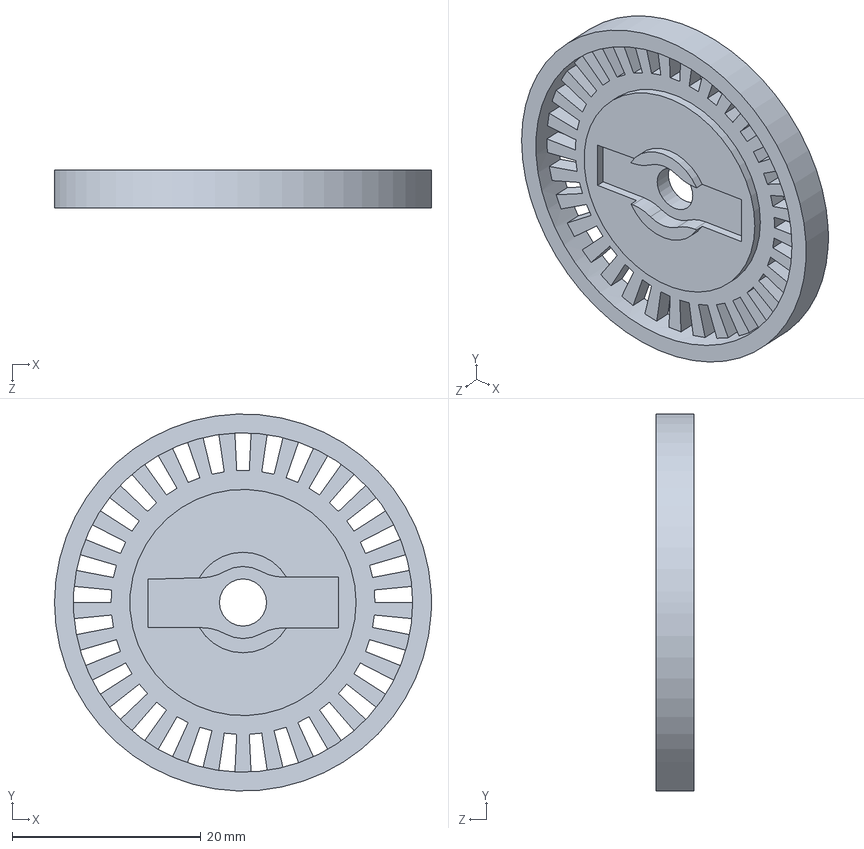
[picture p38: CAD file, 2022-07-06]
Body Design/3dprint/wheel40.SLDPRT
40.0 x 40.0 x 4.00 mm

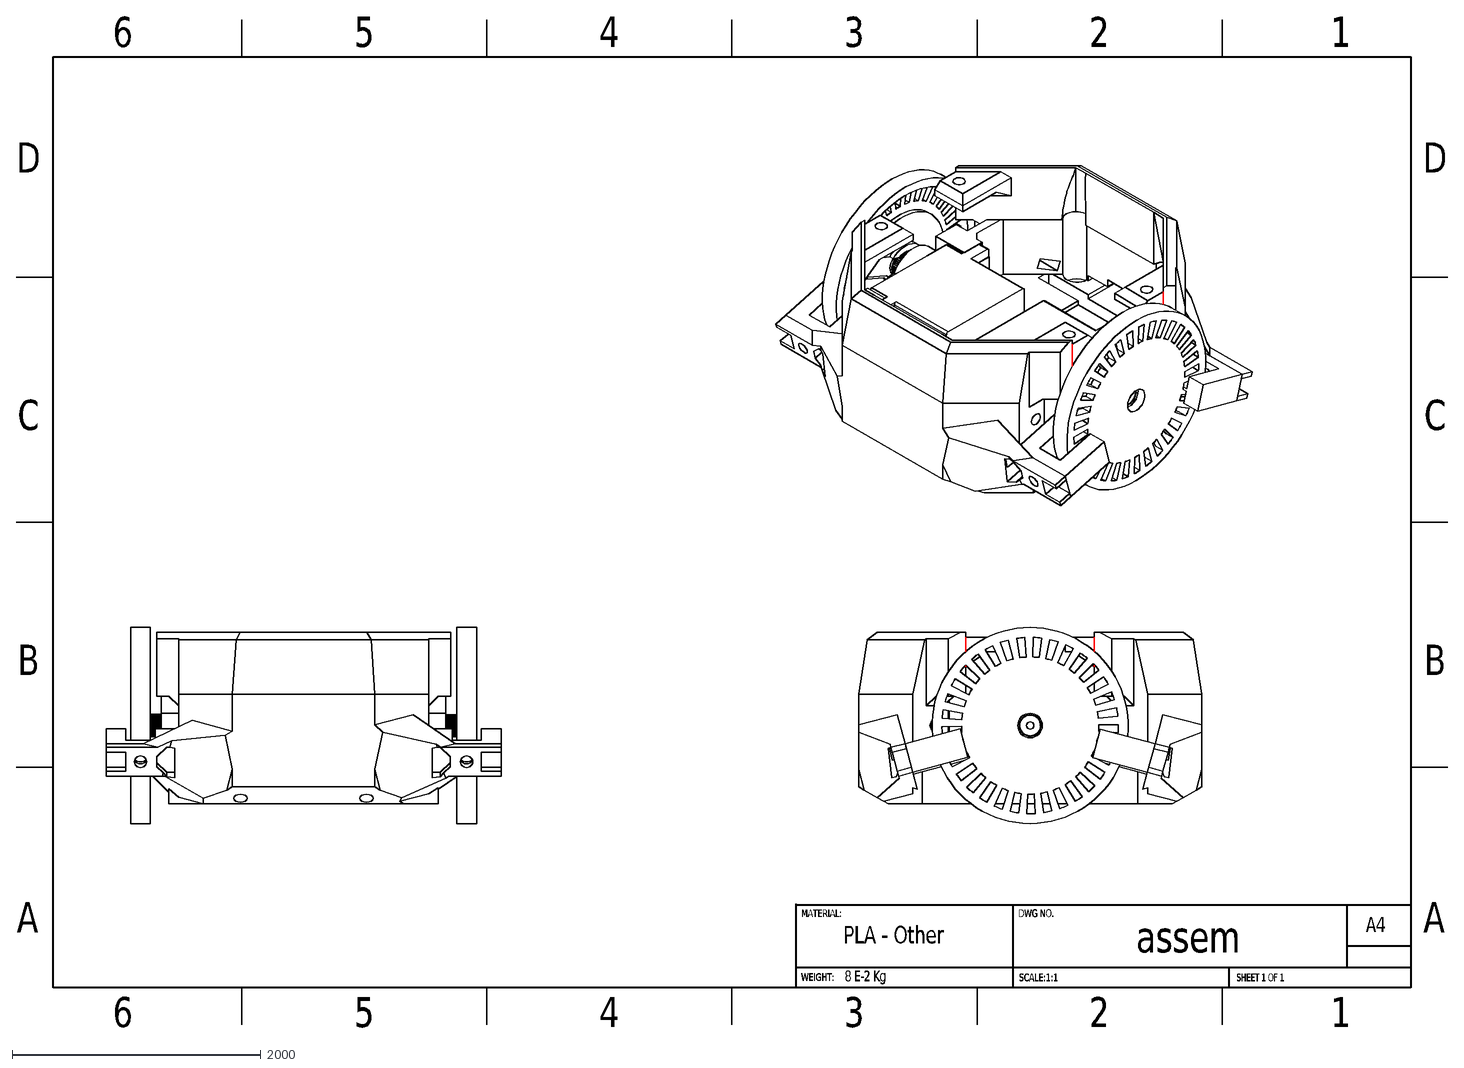
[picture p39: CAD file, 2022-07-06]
Body Design/drawings/assem.DXF
A
B
C
D
6
5
4
3
2
1
MATERIAL:
DWG NO.
SCALE:1:1
SHEET 1 OF 1
A4
WEIGHT:
assem
8 E-2 Kg
PLA - Other

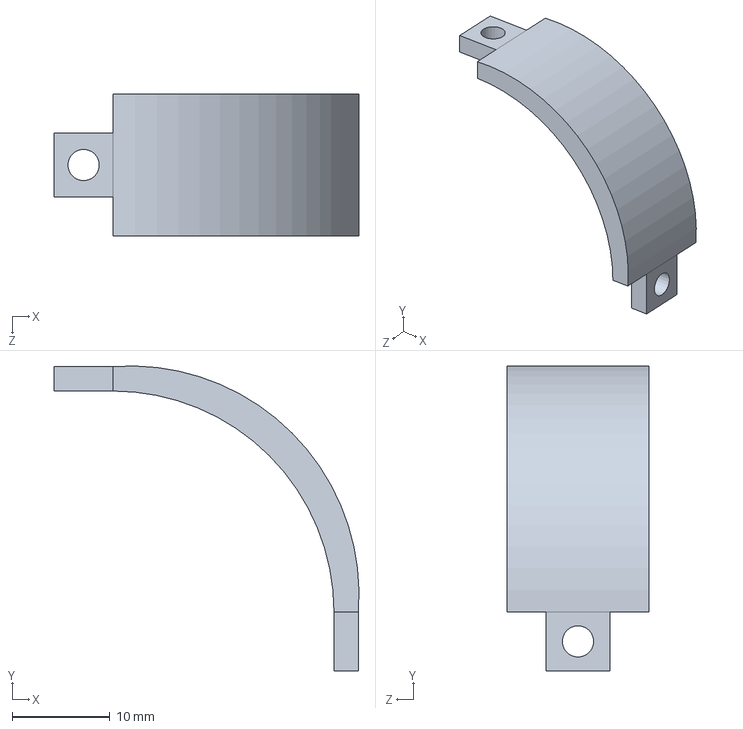
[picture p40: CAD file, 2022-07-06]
Body Design/encoders_holder2.SLDPRT
31.2 x 31.2 x 14.5 mm

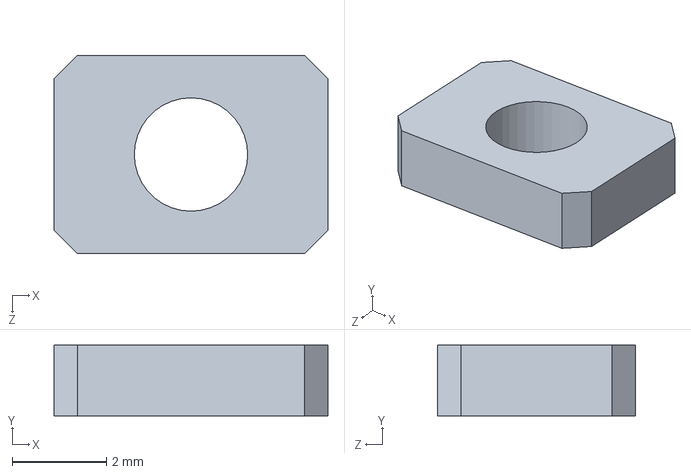
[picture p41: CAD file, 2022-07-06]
Body Design/laser_cut/encoder_housing/Part1.SLDPRT
5.80 x 1.50 x 4.20 mm

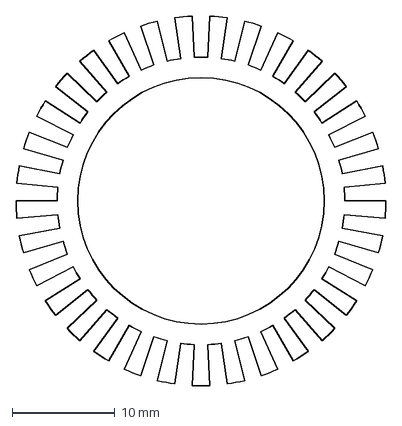
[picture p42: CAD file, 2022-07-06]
Body Design/laser_cut/wheel40.DXF
36.0 x 36.0 mm

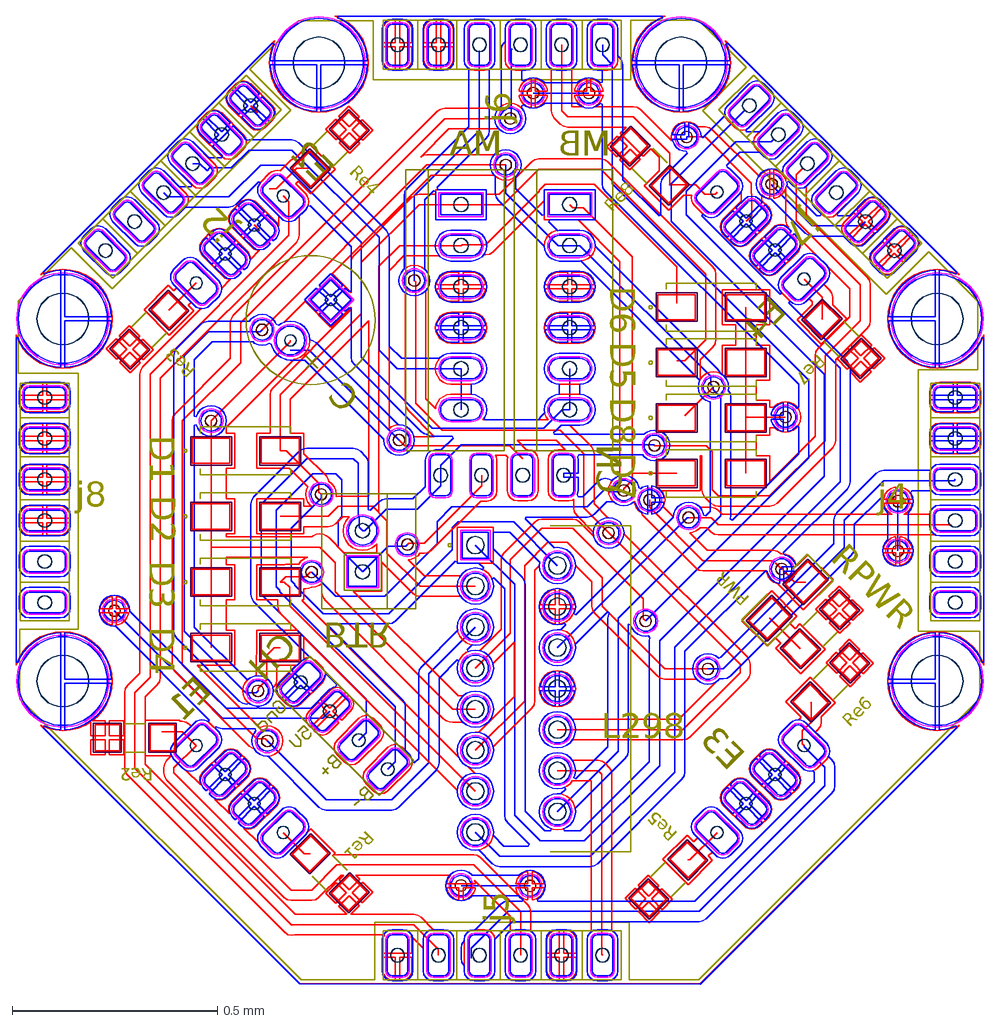
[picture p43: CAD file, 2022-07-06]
Circuits PCB Design/Bottom/stencil/holes_btm.DXF
j8
j2
j6
j7
j4
j5
E4
E2
E3
E1
Re8
Re7
Re6
Re5
Re4
Re3
Re2
Re1
CH
CN
RPWR
C
PWR
BTR
MB
MA
L298
D1
D8
D7
D6
D5
D4
D3
D2

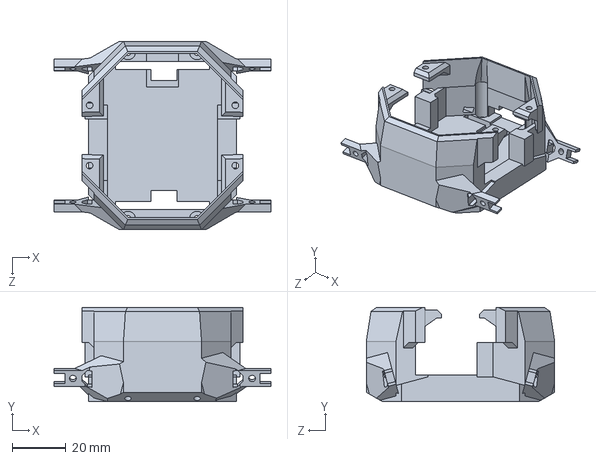
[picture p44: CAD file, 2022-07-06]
Body Design/3dprint/base.SLDPRT
80.6 x 35.0 x 70.0 mm

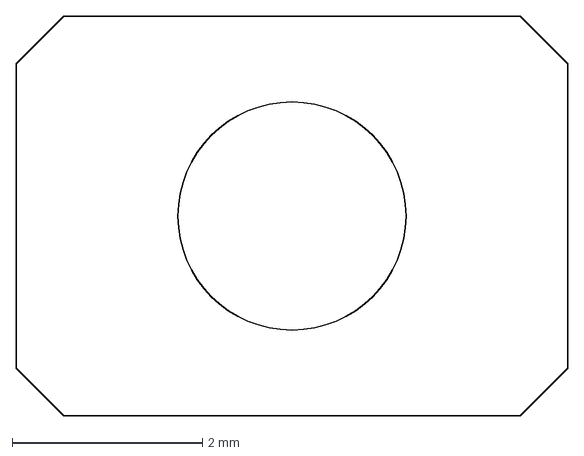
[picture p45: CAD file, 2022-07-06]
Body Design/laser_cut/encoder_housing_2.DXF
5.80 x 4.20 mm

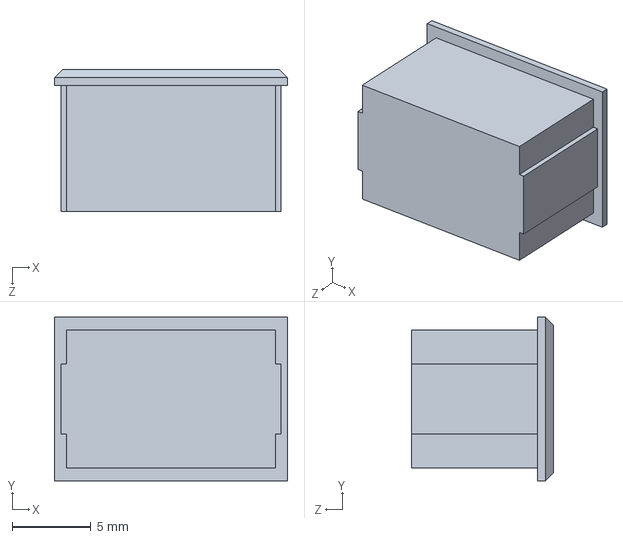
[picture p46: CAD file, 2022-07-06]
Body Design/on_off.SLDPRT
14.8 x 10.4 x 9.00 mm

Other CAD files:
Circuits PCB Design/Top/main.DWG
Circuits PCB Design/Top/stencil/main.DWG
Circuits PCB Design/Top/stencil/holes3.DWG
Body Design/3dprint/ver3/base_2.STL
Circuits PCB Design/Top/stencil/holes2.DWG
Body Design/3dprint/base.STL
Body Design/3dprint/wheel40.STL
Body Design/503450.SLDPRT
Body Design/504040.SLDPRT
Body Design/504045.SLDPRT
Body Design/Microservo horn.SLDPRT
Body Design/STACK_ASM.SLDDRW
Body Design/Workspace.sldprt
Body Design/assem.SLDDRW
Body Design/base.SLDPRT
Body Design/circ.SLDPRT
Body Design/circ_correct_dim.SLDPRT
Body Design/drawings/assem.SLDDRW
Body Design/encoders_holder.SLDPRT
Body Design/laser_cut/encoder_housing.DXF
Body Design/photo_interrupter.SLDPRT
Body Design/scene_obstacle.SLDPRT
Body Design/sg90.SLDPRT
Body Design/wheel40.SLDDRW
Body Design/wheel40.SLDPRT
Circuits PCB Design/Top/stencil/holes.DWG
Circuits PCB Design/Top/stencil/holes4.DWG
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

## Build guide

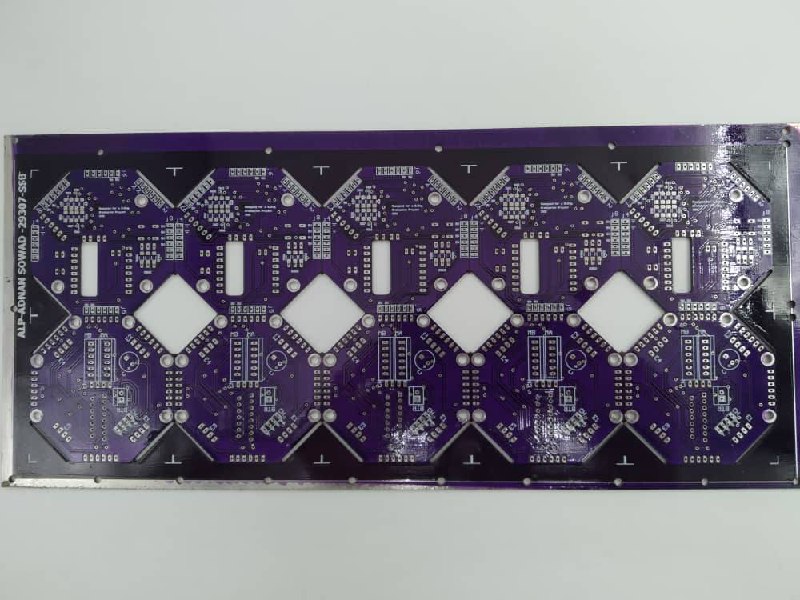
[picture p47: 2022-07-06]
Images/circuits_manufacturing results_1.jpg

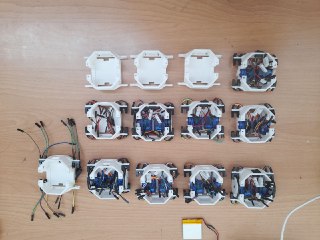
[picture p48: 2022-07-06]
Images/assembling process.jpg

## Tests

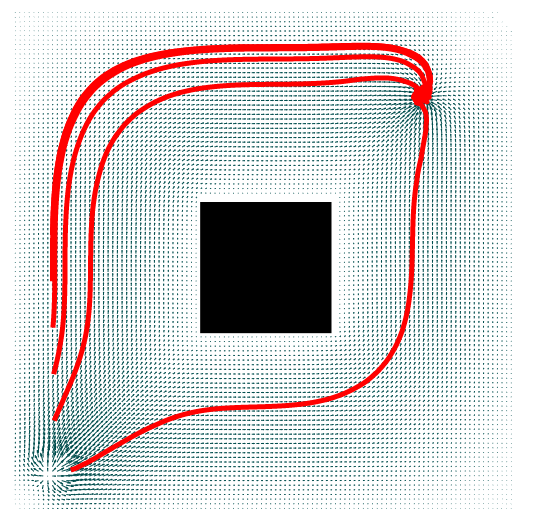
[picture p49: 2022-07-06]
Images/PDE result for a square map.PNG

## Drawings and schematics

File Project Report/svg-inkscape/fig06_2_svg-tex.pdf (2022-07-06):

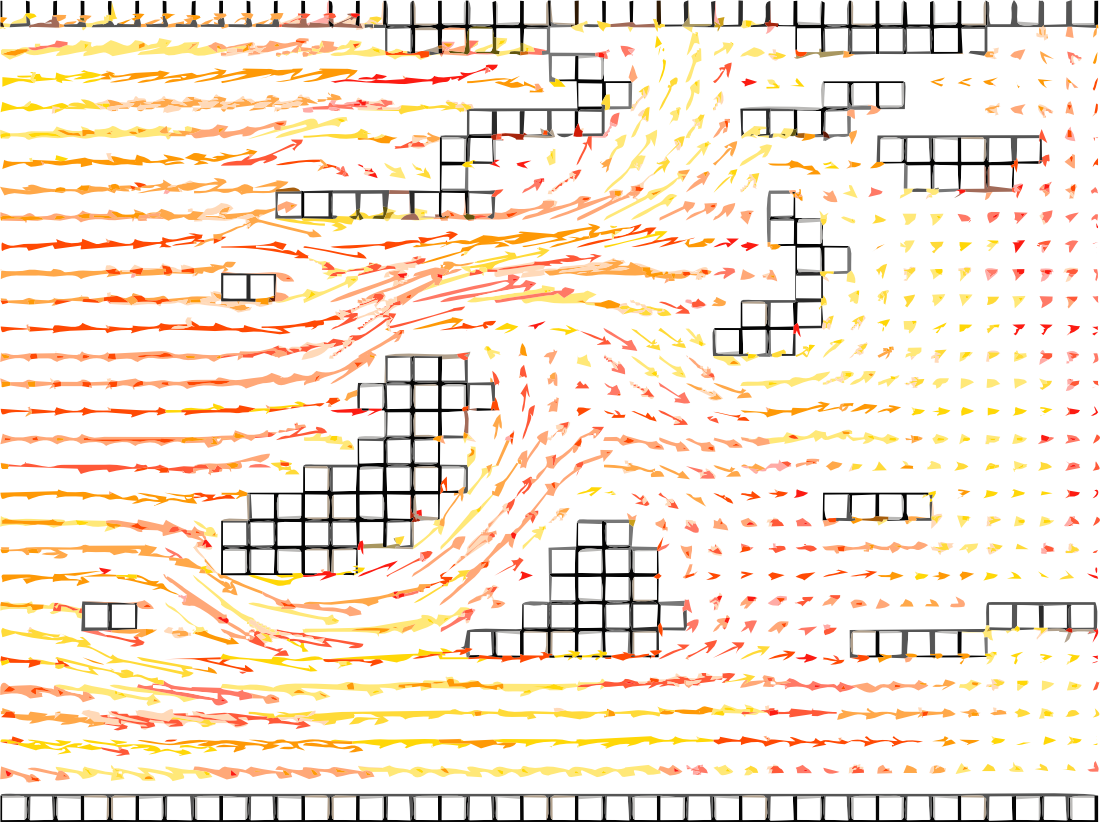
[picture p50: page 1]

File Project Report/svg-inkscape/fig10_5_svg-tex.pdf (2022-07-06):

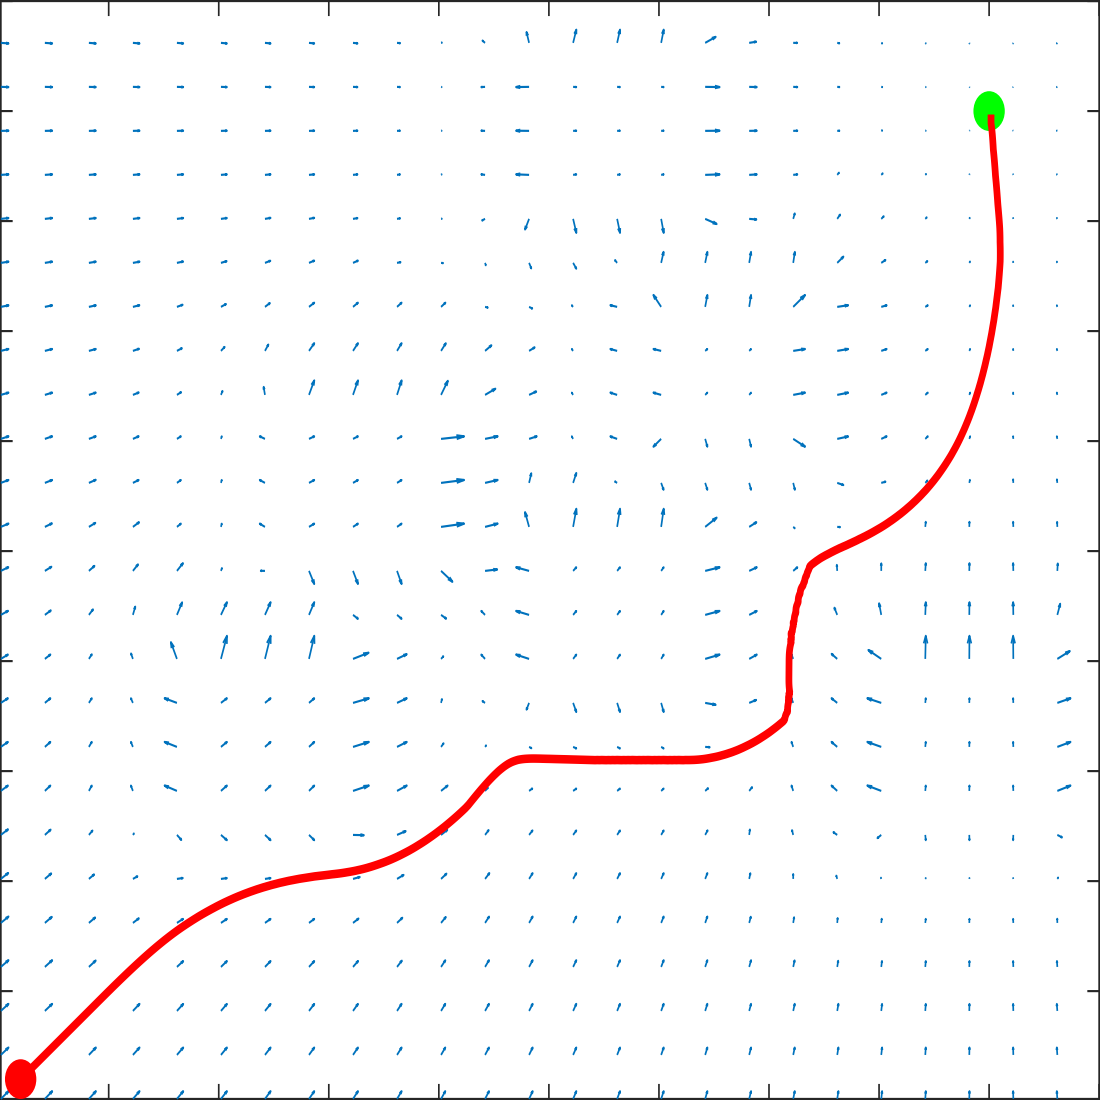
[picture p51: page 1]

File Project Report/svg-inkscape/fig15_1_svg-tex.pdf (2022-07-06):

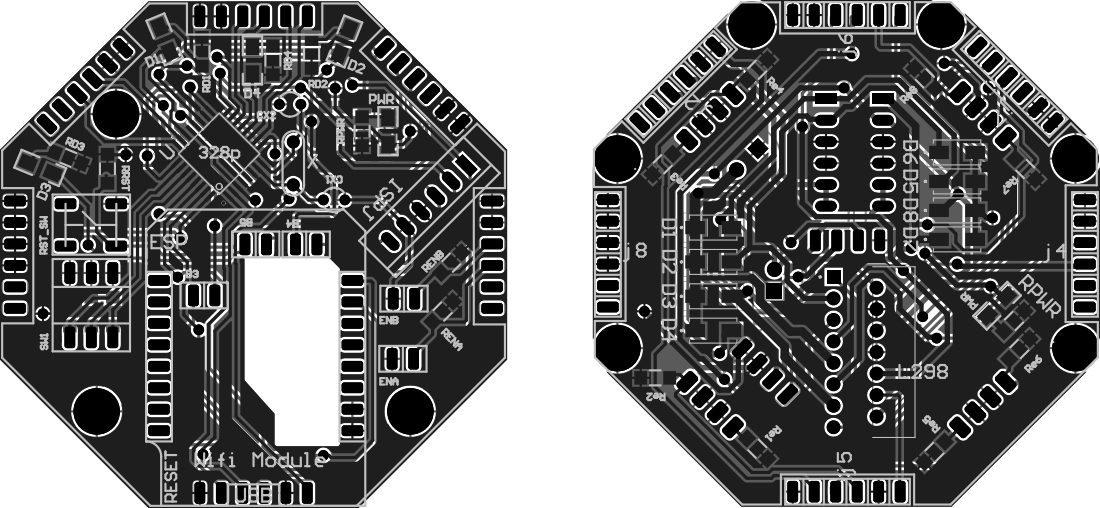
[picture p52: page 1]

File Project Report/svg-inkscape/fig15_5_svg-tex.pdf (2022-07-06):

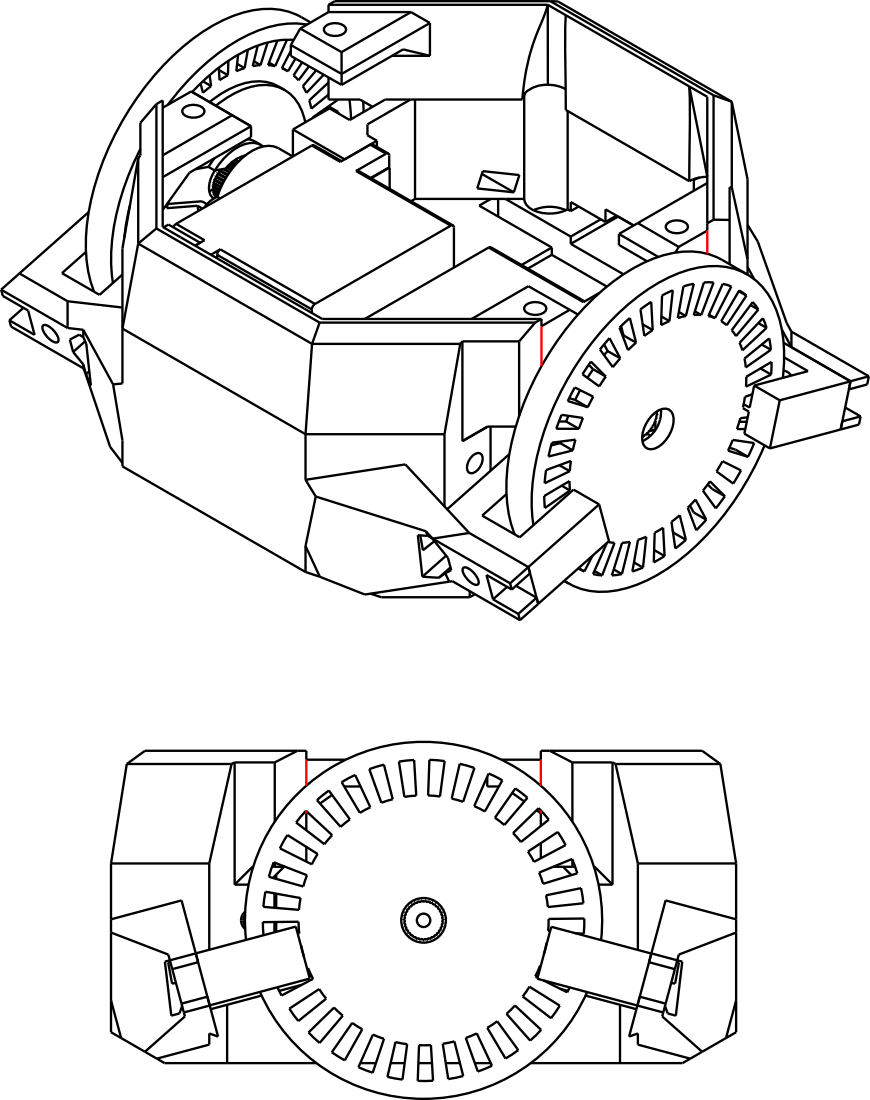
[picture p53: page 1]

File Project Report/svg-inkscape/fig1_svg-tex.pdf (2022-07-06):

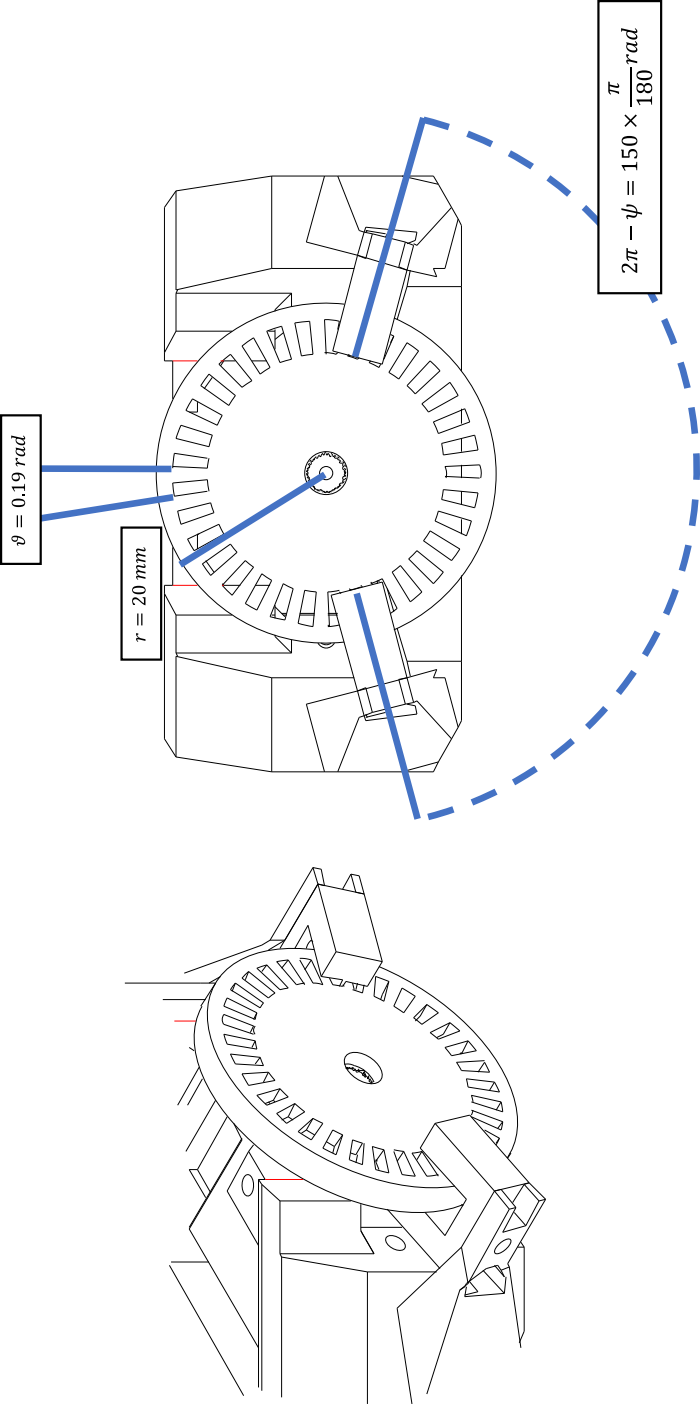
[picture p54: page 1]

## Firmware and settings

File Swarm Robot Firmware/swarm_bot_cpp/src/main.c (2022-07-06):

#include <__swarm_wold__.h>

#include <__kinematics__.h>

int main (void)
{
	/* Insert system clock initialization code here (sysclk_init()). */
	cli();
	board_init();
	DDRB = 0xFF;
	DDRD = 0b01100010;
	
	struct _theta te;
	struct pos p;
	struct pos_dot _p;
	struct _i_pos _i_p;
	struct _omega w;
	te.left = 0;
	te.right = 0;
	w.wl = 0;
	w.wr = 0;
	uint16_t DT = 100;
	uint32_t t_prev = 0;
	sei();
	while (1)
	{
		_set_speed(MA, 200);
		_set_speed(MB, 200);
		_update_omega(&w);
		_i_p = _omega_to_intertial(&w);
		printf("(%f , ", _i_p.v);
		printf(" %f)\n", _i_p.w);
		_delay_ms(100);
		//_set_speed(MA, 80);
		//while(1)
		//{
		//	printf("+(%d,", (int)(_omega_from_encA()*57.29577));
		//	printf(" %d )\n",(int)( _omega_from_encB()*57.29577));
		//	_delay_ms(100);
		//	if(_ticksA() < 0)
		//	{
		//		break;
		//	}
		//}
	}
	return 0;
}
